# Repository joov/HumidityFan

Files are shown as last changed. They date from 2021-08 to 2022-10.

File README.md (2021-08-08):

# Humidity Fan Project

## Intention

This project is a low cost solution for rooms with high humidity like

- garden houses
- cellar rooms
- bath rooms

to get some air circlulation. It is inspired by [this](https://create.arduino.cc/projecthub/LIMPINGLIM/humidity-sensor-controlled-bathroom-exhaust-fan-27131f) project.

You have to be aquainted with:

- Using arduino
- Soldering
- 3D printing

if you want to build a device of your own

## Main components

The system consists of these main parts:

- PC case fan to get the air with high humidity out of the room
- Two humidity and temerature sensors (DHT11) to get information about inner and and outer conditions
- Arduino nano to control everything
- A board to fit all electronics onto
- A small display to see what the controller is doing

Aditionally there are a few 3D printed components to fit it all together:

- Case of arduino board, inner sensor and display
- Case for outer humidity sensor
- Adapter to fit the PC case fan to a System 125 ventilation pipe (customizable)

## Part list

Please note that I do not guarantee this part list to be exhaustive.

|part|qty|I used|remark|
|---|---|---|---|
|Arduino nano|1||I recommend the original ones|
|DHT-11 sensor|2|[these](https://www.amazon.de/gp/product/B07Q3H3Y68)|plain ones, not already soldered to board|
|MOSFET|1|[this](https://www.amazon.de/gp/product/B08GFD7F9V)||
|OLED display|1|[this](https://www.amazon.de/gp/product/B074N9VLZX)||
|2 Pin PCB Mount Screw Terminal Block|1|[a set](https://www.amazon.de/gp/product/B07MM8RJLW)|the set contains much more than you need
|3 Pin PCB Mount Screw Terminal Block|3||see above|
|PC case fan|1|[this](https://www.amazon.de/gp/product/B07GB16RK7)||
|small peace of breadboard|||approx 6x7 holes, for outer sensor||
|wires|||

Furthermore you need:

- the board (see [here](./Circuit)
- cases and fan adapter (see [here](./3DPrint)

Lastly there is an arduino sketch to make everything going [here](./Sketch)

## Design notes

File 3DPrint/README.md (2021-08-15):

# 3DPrint

All designs are customizable. 

For the cases, the board is alway sitting on the "lid"-part, which also has mounting holes to fix it on a wall etc.

The _inner_box_lid_ has to be turned 180 around the y-axis before printing!

For the outer sensor the board just glued to the lid part.

For fan-adapter you should consider calibrating your printers x/y-axis (mine did not fit before calibrating)

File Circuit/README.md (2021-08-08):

# Circuit

## Arduino

The circuit was designed using [KiCad](https://www.kicad.org/). The layout was done using [freerouting](https://github.com/freerouting/freerouting) as described [here](https://techexplorations.com/blog/kicad/blog-kicad-5-how-to-use-the-freerouting-autorouter)

I printed the boards with [Aisler](https://aisler.net) who do a pretty good job, but have a minimum batch size of 3. The file you have to use is `HumidityFan.kicad_pcb`.

## Outer sensor

For the outer sensor you can just solder the sensor to one side of a small 7x6 breadboard (I cut mine from a bigger one), solder a  Pin PCB Mount Screw Terminal Block to the opposite side and connect the pins using silver wire (note that one pin of the DHT11 is not used).

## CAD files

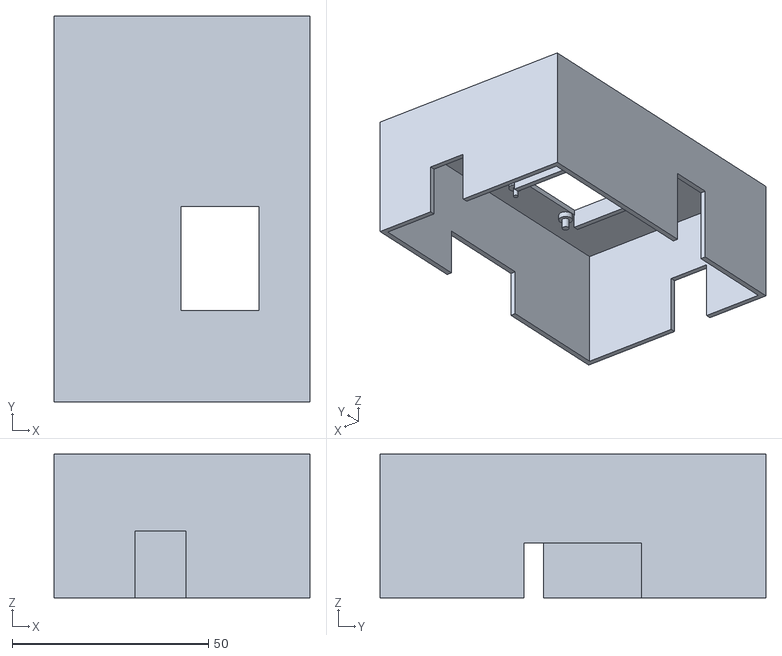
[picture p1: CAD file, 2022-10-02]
3DPrint/inner_box_lid.stl
65.2 x 98.2 x 36.6

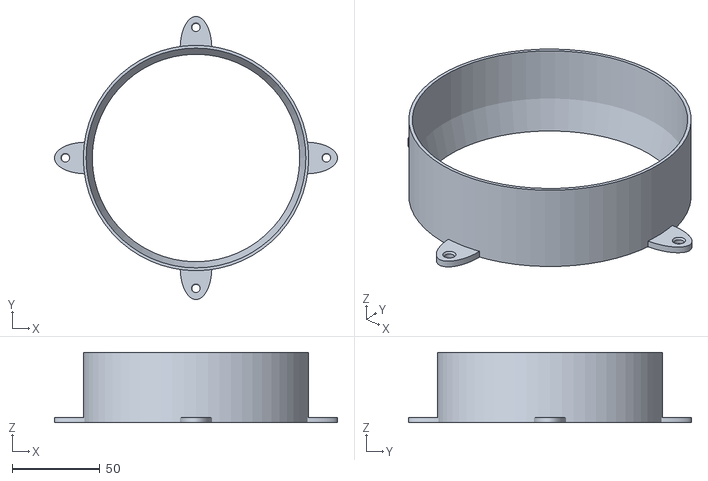
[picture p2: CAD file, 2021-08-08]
3DPrint/Fan-to-125-adapter.stl
161.0 x 161.0 x 40.0

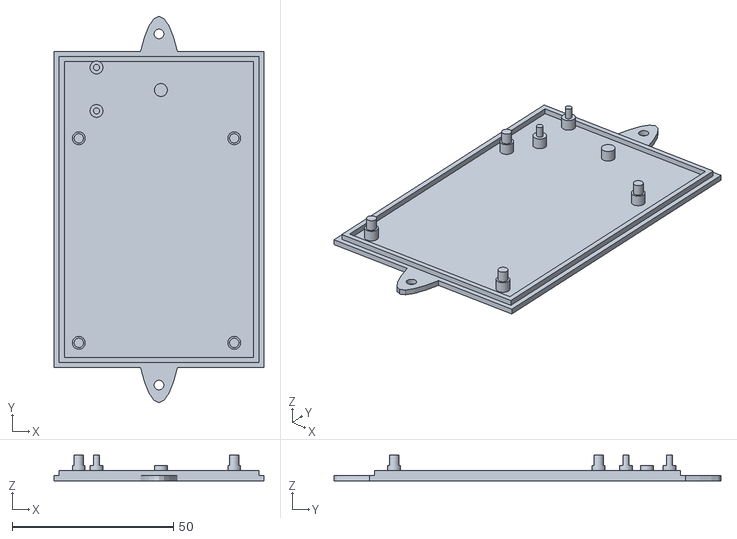
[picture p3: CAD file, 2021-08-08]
3DPrint/inner_box_base.stl
65.2 x 120.0 x 8.00

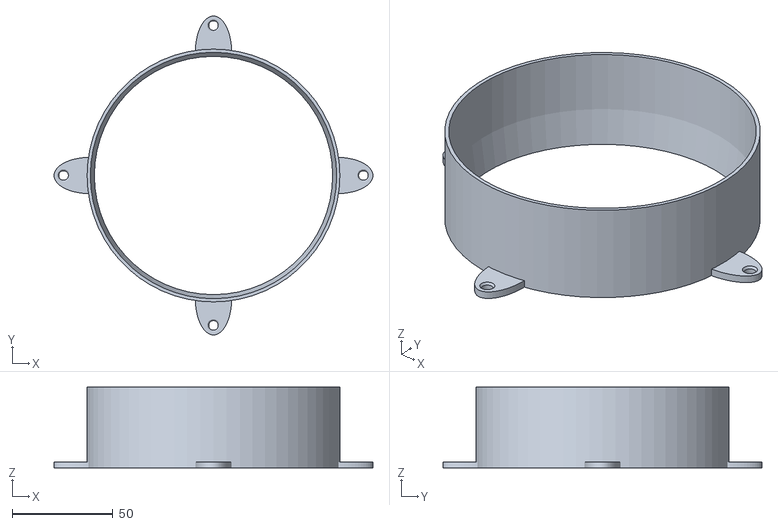
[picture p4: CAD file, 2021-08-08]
3DPrint/Fan-to-122-adapter.stl
158.0 x 158.0 x 40.0

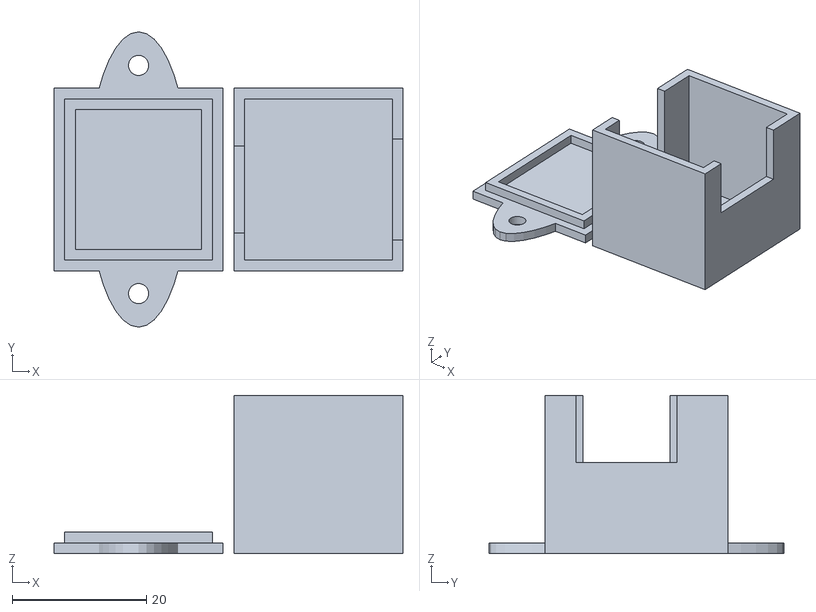
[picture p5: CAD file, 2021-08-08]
3DPrint/outer_box.stl
52.0 x 44.0 x 23.6

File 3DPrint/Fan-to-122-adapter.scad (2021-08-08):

$fn=60;
inner_d1=118; // diameter of lower fitting
inner_d2=122; // diameter of adapter piece


wall_thickness=1.6;
overall_height=40;
adapter_height=25; // Height of adapter piece

hole_distance=105; // assuming holes are in square position
hole_diag_distance=sqrt(2.0)*hole_distance;
hole_width=4.7;  // Diameter of screw hole
hole_bevel=6;    // Diameter of bevel for srew hole

assert(hole_diag_distance+2*hole_bevel > inner_d2+2*wall_thickness, "Hole spacing too small!");

difference() {
    union() {
        cylinder(h=overall_height,d=inner_d2+2*wall_thickness);
        for (i = [inner_d2/2,-inner_d2/2]){
          translate([i,0,0])resize([6*hole_bevel,3*hole_bevel])cylinder(h=3,d=40);
        translate([0,i,0])resize([3*hole_bevel,6*hole_bevel])cylinder(h=3,d=40);
        }
        
    }
    cylinder(h=overall_height-adapter_height,d1=inner_d1,d2=inner_d2);
    translate([0,0,overall_height-adapter_height])cylinder(h=adapter_height,d=inner_d2);
    for (i = [hole_diag_distance/2,-hole_diag_distance/2]){
      translate([i,0,0]) {
        cylinder(h=4,d=hole_width);
        translate([0,0,2]) cylinder(h=1.01,d1=hole_width,d2=hole_bevel);
      }
      translate([0,i,0]) {
        cylinder(h=4,d=hole_width);
        translate([0,0,2]) cylinder(h=1.01,d1=hole_width,d2=hole_bevel);
      }
    }
}

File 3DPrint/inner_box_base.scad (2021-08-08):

//Procedural Project Box Screws

//40mm x 60 board size

inside_width = 62;
inside_length = 95;
inside_height = 30;
pole_height=8;
pole_wall_dist = 4.5;

$fn=40;

wall_thickness=1.6;

module doPole(trans=[0,0], dia=2.9, base=4, ph=pole_height) {
    translate([2*wall_thickness,2*wall_thickness])translate(trans) {
        cylinder(d=dia,h=ph);
        cylinder(d=base,h=3*wall_thickness);
    }
        
}



union(){
//translate([0,inside_length+2*wall_thickness,0])rotate([0,0,90])mirror([1,1,0])difference() {
//    cube([inside_width+2*wall_thickness, 
//        inside_length+2*wall_thickness,
//        inside_height+wall_thickness]);
//    translate([wall_thickness,wall_thickness,wall_thickness])cube([inside_width, 
//        inside_length,
//        inside_height]);
//
//    translate([19+wall_thickness,-5,inside_height+wall_thickness-12])cube([9,10,12]);        
//
// translate([-5,53+wall_thickness,wall_thickness])cube([10,17,22]);
// translate([inside_width+2*wall_thickness-5,42+wall_thickness,wall_thickness+inside_height-14])cube([10,27,14]);
//
// translate([24+wall_thickness,inside_length-5,wall_thickness+inside_height-15])cube([12,10,15]);
//    
//}




translate([-inside_width-3*wall_thickness,0,0]) {

  union() {
    cube([inside_width+2*wall_thickness, 
        inside_length+2*wall_thickness,
        wall_thickness]);

    difference(){translate([wall_thickness,wall_thickness,wall_thickness])cube([inside_width, 
        inside_length,
        wall_thickness]);
      
         translate([2*wall_thickness,2*wall_thickness,wall_thickness]) cube([inside_width-2*wall_thickness, 
        inside_length-2*wall_thickness,
        wall_thickness]);
    }
    translate([inside_width/2+wall_thickness,inside_length/2+wall_thickness])difference(){
        resize([20,inside_length+25])cylinder(d=10,h=wall_thickness);
        translate([0,-inside_length/2-7])cylinder(d=3,h=10*wall_thickness);
        translate([0,inside_length/2+7])cylinder(d=3,h=10*wall_thickness);
    }
    
}


union(){
    
    
    // Poles for main board
    doPole([pole_wall_dist, pole_wall_dist]) ;
    doPole([pole_wall_dist+48.26,pole_wall_dist]) ;
    doPole([pole_wall_dist, pole_wall_dist+63.5]) ;
    doPole([pole_wall_dist+48.26, pole_wall_dist+63.5]) ;

    // Poles for MOSFET
    doPole([10, 76.5], 1.9, 4);
    doPole([10, 90], 1.9, 4) ;
    doPole([30, 83], 1.9, 4, 3*wall_thickness);
    
  }
  }
}
    

        

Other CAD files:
3DPrint/Fan-to-125-adapter.scad
3DPrint/inner_box_lid.scad
3DPrint/outer_box.scad

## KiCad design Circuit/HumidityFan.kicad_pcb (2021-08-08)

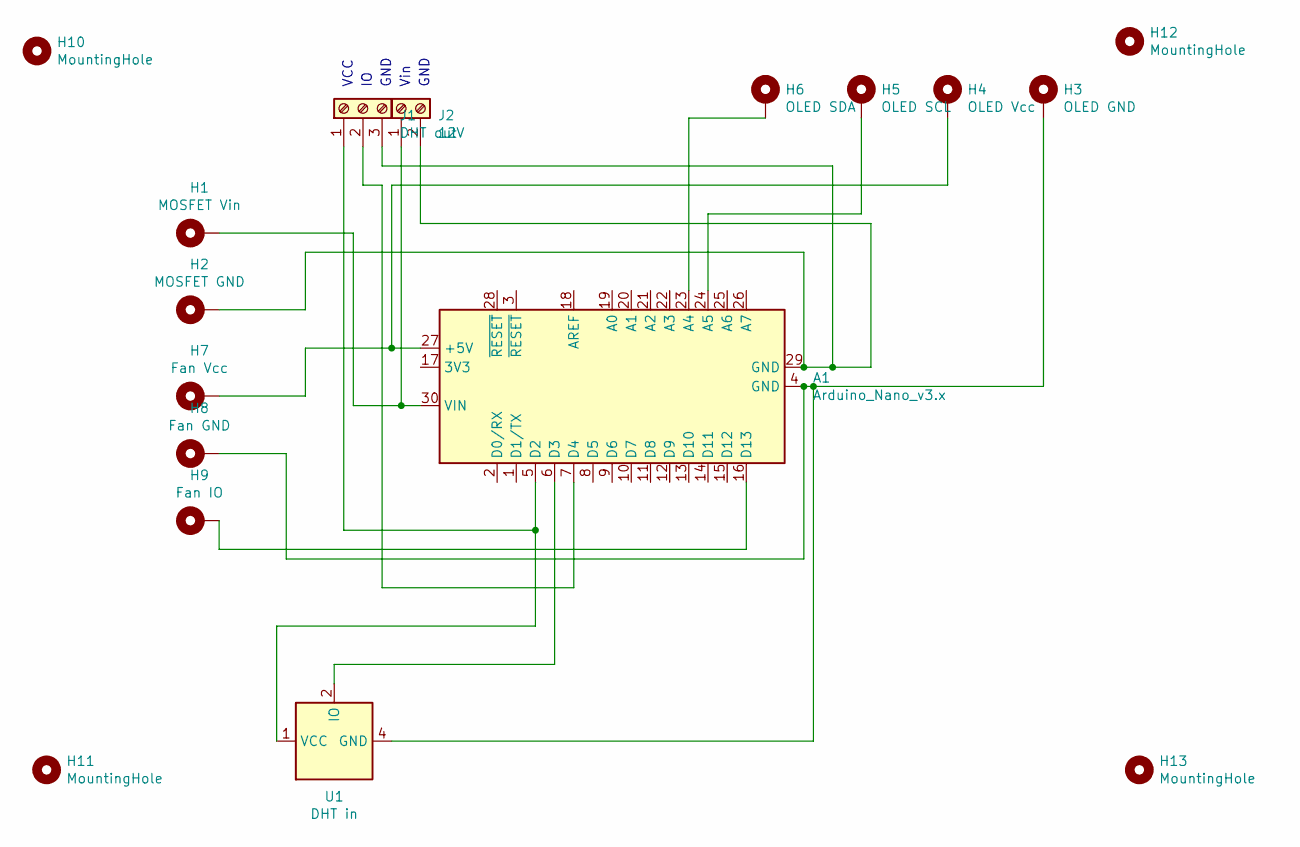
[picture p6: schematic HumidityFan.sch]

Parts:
A1: Arduino_Nano_v3.x; Arduino_Nano
H1: MOSFET Vin; SolderWire-1sqmm_1x01_D1.4mm_OD2.7mm
H2: MOSFET GND; SolderWire-1sqmm_1x01_D1.4mm_OD2.7mm
H3: OLED GND; SolderWire-0.5sqmm_1x01_D0.9mm_OD2.1mm
H4: OLED Vcc; SolderWire-0.5sqmm_1x01_D0.9mm_OD2.1mm
H5: OLED SCL; SolderWire-0.5sqmm_1x01_D0.9mm_OD2.1mm
H6: OLED SDA; SolderWire-0.5sqmm_1x01_D0.9mm_OD2.1mm
H7: Fan Vcc; SolderWire-0.5sqmm_1x01_D0.9mm_OD2.1mm
H8: Fan GND; SolderWire-0.5sqmm_1x01_D0.9mm_OD2.1mm
H9: Fan IO; SolderWire-0.5sqmm_1x01_D0.9mm_OD2.1mm
H10, H11, H12, H13: MountingHole; MountingHole_3mm
J1: DHT out; TerminalBlock_Altech_AK300-3_P5.00mm
J2: 12V; TerminalBlock_Altech_AK300-2_P5.00mm
U1: DHT in; Aosong_DHT11_5.5x12.0_P2.54mm

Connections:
unnamed: A1.4 (GND), H3.1, H8.1, U1.4 (GND)
unnamed: A1.5 (D2), J1.1, U1.1 (VCC)
unnamed: A1.6 (D3), U1.2 (IO)
unnamed: A1.7 (D4), J1.2
unnamed: A1.16 (D13), H9.1
unnamed: A1.23 (A4), H6.1
unnamed: A1.24 (A5), H5.1
unnamed: A1.27 (+5V), H4.1, H7.1
unnamed: A1.29 (GND), H2.1, J1.3, J2.2
unnamed: A1.30 (VIN), H1.1, J2.1

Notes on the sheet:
VCC
GND
Vin

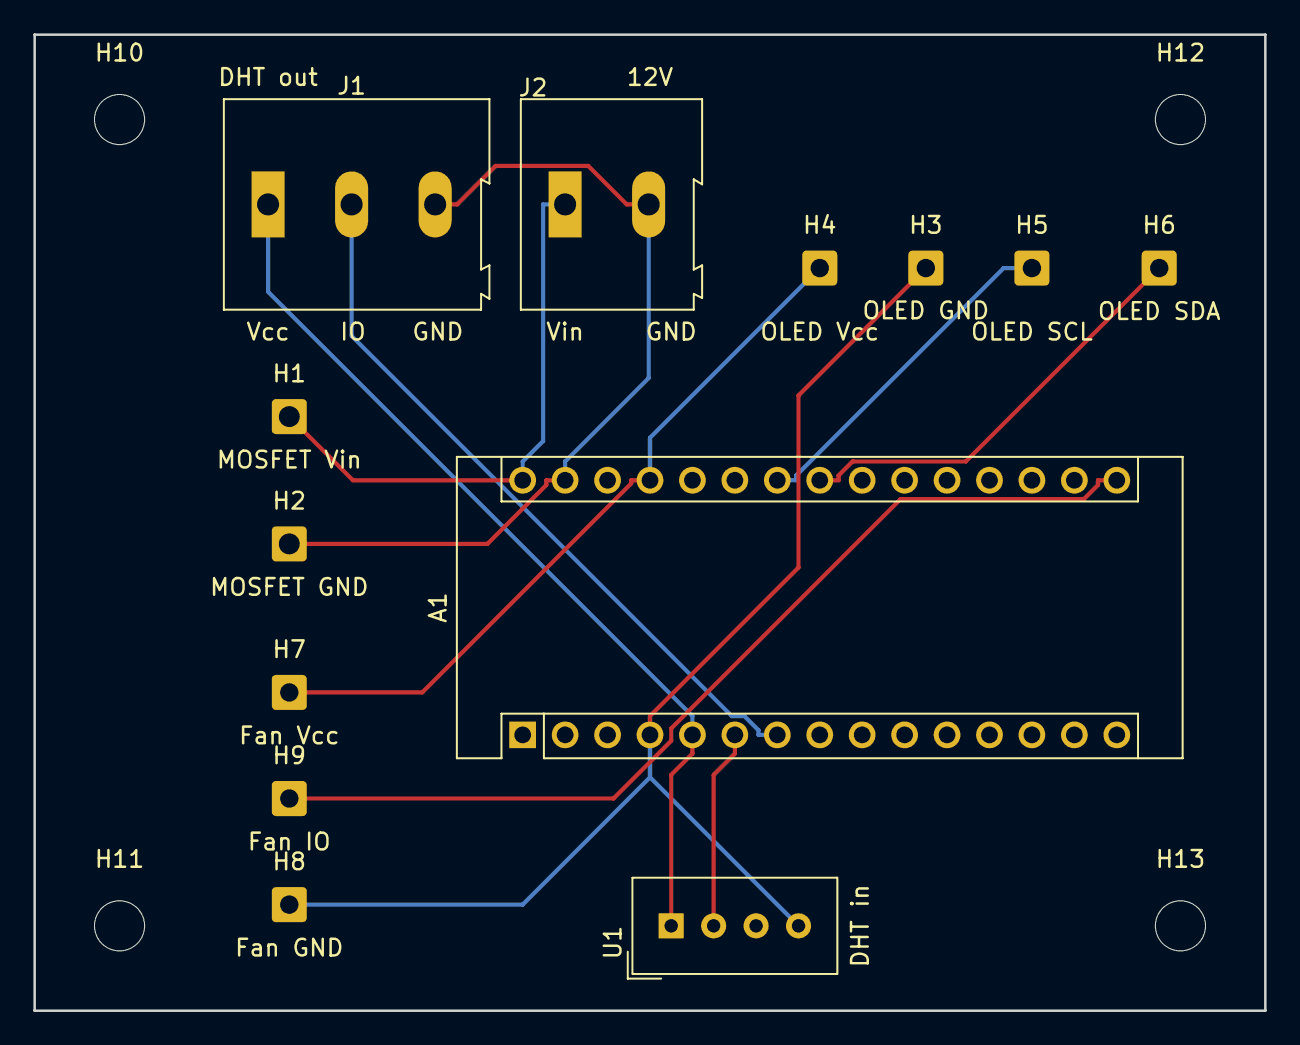
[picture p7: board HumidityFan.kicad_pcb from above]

Board: 2 copper layers, 73.7 x 58.4 mm, 17 parts (0 on the bottom side), 10 nets.

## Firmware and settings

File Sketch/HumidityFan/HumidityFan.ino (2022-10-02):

// Defines for DHT
#include <SimpleDHT.h>

//Declaring digital pin no 2 as the dht11 data pin

int pinDHT11_inner = 3;
int pinDHT11_outer = 4;
int DHTpower = 2;
int fanPower = 13;

float a = 7.5;
float b = 237.3;
float c = 6.1078;

int minTemp=5;

unsigned long fanTime=1500000;    // 10 minutes
unsigned long delayTime=1800000-fanTime; // 30 minutes-fanTime


SimpleDHT11 dht11;


// Defines for OLED SDD1306
#include <SSD1306Ascii.h>
#include <SSD1306AsciiAvrI2c.h>

// 0X3C+SA0 - 0x3C or 0x3D
#define I2C_ADDRESS 0x3C

// Define proper RST_PIN if required.
#define RST_PIN -1

SSD1306AsciiAvrI2c oled;

void setup() {

  // Setup DHT
  pinMode(DHTpower, OUTPUT);
  digitalWrite(DHTpower, LOW);

  Serial.begin(9600);   

  // Setup FAN
  pinMode(fanPower, OUTPUT);
  Serial.println("============ Testing Fan... ===============");

  digitalWrite(fanPower, HIGH);
  delay(5000);
  digitalWrite(fanPower, LOW);
  Serial.println("============ ...End Test Fan ===============");

  // Setup OLED 1306
  #if RST_PIN >= 0
    oled.begin(&Adafruit128x64, I2C_ADDRESS, RST_PIN);
  #else // RST_PIN >= 0
    oled.begin(&Adafruit128x64, I2C_ADDRESS);
  #endif // RST_PIN >= 0
  // Call oled.setI2cClock(frequency) to change from the default frequency.

  oled.setFont(Callibri11);
  oled.clear();
  oled.println("Starting...");
}

void loop() {
  delay(1000);
  oled.clear();
  RHcheck();                        //check Humidity Level
  Serial.print("Waiting... ");Serial.print(delayTime/1000); Serial.println(" sec");
  oled.print("Waiting ");oled.print((unsigned long)delayTime/1000/60);oled.println(" min...");
  delay(delayTime);                    
  }


/**
 * Calculate Dew Point
 * cf https://www.wetterochs.de/wetter/feuchte.html
 */
float dew_point(byte temp, byte hum) {
  float t = (float) temp;
  float sdd = c * pow(10,(a*t)/(b+t));

  float dd = ((float) hum) * sdd / 100.0 ;
  float v = log10(dd/c) ;
  return b*v/(a-v) ;
}

void RHcheck() {                    //Check Humidity Level Function
  digitalWrite(DHTpower, HIGH);     //On Humidity Sensor
  delay(5000);
  Serial.println("============ Check Humidity ===============");
  delay(1000);
  Serial.println("DHT11 readings...");
   
  byte temp_inner = 0;
  byte hum_inner = 0;
  byte temp_outer = 0;
  byte hum_outer = 0;
  int err = SimpleDHTErrSuccess;

  //This bit will tell our Arduino what to do if there is some sort of an error at getting readings from our sensor
  if ((err = dht11.read(pinDHT11_inner, &temp_inner, &hum_inner, NULL)) != SimpleDHTErrSuccess) {

    oled.print("IN ERROR: ");oled.println(err);
    Serial.print("No reading from inner sensor, err="); Serial.println(err);delay(1000);
    return;
  }

  //This bit will tell our Arduino what to do if there is some sort of an error at getting readings from our sensor
  if ((err = dht11.read(pinDHT11_outer, &temp_outer, &hum_outer, NULL)) != SimpleDHTErrSuccess) {
    oled.print("OUT ERROR: ");oled.println(err);
    Serial.print("No reading from outer sensor, err="); Serial.println(err);delay(1000);
    return;
  }

  float tp_inner = dew_point(temp_inner, hum_inner) ;
  float tp_outer = dew_point(temp_outer, hum_outer) ;
  
  digitalWrite(DHTpower, LOW);     //Switch off Humidity Sensor

  oled.print("IN:    ");
  oled.print((int)temp_inner); oled.print(" C, ");
  oled.print((int)hum_inner); oled.print(" %, ");
  oled.print("TP: ");oled.print((int)tp_inner); oled.println(" C");
  oled.print("OUT: ");
  oled.print((int)temp_outer); oled.print(" C, ");
  oled.print((int)hum_outer); oled.print(" %, ");
  oled.print("TP: ");oled.print((int)tp_outer); oled.println(" C");

  if (tp_inner > tp_outer) {  // tp_outer has to be really smaller to make a difference and avoid unintended increase of humidity
    Serial.println("Dew Point inner is higher ==> fan OK");
  }
  else {
    Serial.println("Dew Point outer is higher ==> fan NOK");
    oled.println("FAN: NOK (dew point)");
    return;
  }
  if (temp_inner<=minTemp || temp_outer<=minTemp) {
    Serial.println("inner or outer Temp to low ==> fan NOK");
    oled.println("FAN: NOK (min temp)");
    return;
  }
  else{
    Serial.println("inner and outer Temp OK ==> fan OK");
  }
  oled.print("Running ");oled.print((unsigned long)fanTime/1000/60);oled.println(" min...");
  delay(500);
  digitalWrite(fanPower, HIGH);
  delay(fanTime);
  digitalWrite(fanPower, LOW);
  
 }

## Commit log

2021-08-15 higher box lid
    [inner_box_lid.scad, inner_box_lid.stl]
2022-10-02 fix: typo
    [inner_box_lid.scad, inner_box_lid.stl]
